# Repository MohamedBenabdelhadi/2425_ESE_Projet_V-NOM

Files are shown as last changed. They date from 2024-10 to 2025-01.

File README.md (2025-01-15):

# 2425-ESE-Projet-V-NOM

Ce projet consiste à créer un robot capable de jouer au chat et la souris avec d'autres robots du même type. Ils joueront sur une table sans bordures et devront donc être capable de détecter les bords de celle-ci.
Les élèves sont chargés de réaliser les schémas électroniques, le routage et la configuration des différents composants choisis pour réaliser ce projet.
Celui-ci est piloté par un microcontrôleur de type STM32.

> Groupe: Mohamed Benabdelhadi, Nouhaila Faris, Oliver Belliard, Valerian Priou.

## Strategie

La stratégie de déplacement retenue a été de détecter les bords de la surface de l'arène grâce à des capteurs de distance à l'avant du robot pointant chacun à 45° de l'axe central du robot, dans des directions opposées. L'idée d'origine consistait à mettre un capteur à l'avant et l'arrière mais suite aux conseils d'un intervenant extérieur, il a été jugé plus judicieux de placer les capteurs dans un même sens pour éviter que le robot tombe de la table dans les cas critiques, comme par exemple lorsque le robot s'approche du bord de la table avec une trajectoire diagonale avec un angle d'attaque très faible.  
  
**En mode souris :** le robot cherche à garder la plus grande distance possible du robot adverse ("chat"), tout en évitant les bords.  
**En mode chat :** le robot cherche à entrer en contact avec le robot adverse ("souris") par collision.  
  
La détection de la position du robot adverse se fait grâce au capteur Lidar qui permet de déterminer une trajectoire en temps réel. La détection de la collision est faite grâce à l'accéléromètre sur le PCB.  
  
Notre logique de direction consiste à réduire la différence entre l'angle où se trouve la cible détectée avec le Lidar puis s'approcher ou s'éloigner de celle ci en fonction du mode.  

## BOM (Bill Of Materials)

### Liste des composants

- Microcontrôleur : STM32G431CBU6 [(ST-Microelectronics)](https://www.st.com/en/microcontrollers-microprocessors/stm32g431cb.html)  
- Quartz 16 MHz [(Farnell : 2853935)](https://fr.farnell.com/multicomp/mcsjk-7u-16-00-10-30-80-b-30/quartz-16mhz-10pf-3-2mm-x-2-5mm/dp/2853935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)  
- Connecteur SWD/STLink [(Farnell : 3226055)](https://fr.farnell.com/harwin/m50-3600742/conn-btb-header-14-voies-2-rangs/dp/3226055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)  
- Driver moteur : ZXBM5210-SP-13 [(Farnell : 3946343)](https://ch.farnell.com/fr-CH/diodes-inc/zxbm5210-sp-13/motortreiber-40-bis-105-c/dp/3946343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)  
- Moteurs : DfRobot FIT0520 ou FIT0521 [(Farnell : 4308214)](https://fr.farnell.com/dfrobot/fit0521/motor-ducteur-cc-34-1-210rpm-6v/dp/4308214)  
- Accéléromètre : ADXL343BCCZ-RL [(Farnell : 4030100)](https://fr.farnell.com/analog-devices/adxl343bccz-rl/acc-l-rom-tre-mems-num-axes-x/dp/4030100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)  
- Régulateur 5V : MP1475S [(Farnell : 3357926)](https://fr.farnell.com/monolithic-power-systems-mps/mp1475sgj-p/conv-dc-dc-sync-buck-500khz-125/dp/3357926)  
- Régulateur 3.3V : BU33SD5WG-TR [(Farnell : 3011248)](https://fr.farnell.com/rohm/bu33sd5wg-tr/ldo-fixe-3-3v-0-5a-40-a-105-c/dp/3011248)  
- Batterie NIMH 7.2V 1.3Ah [(RS : 777-0377)](https://fr.rs-online.com/web/p/blocs-batteries-rechargeables/7770377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)  
- Capteur bordure : GP2Y0A41SK0F [(RS : 666-6568)](https://fr.rs-online.com/web/p/capteurs-optiques-reflechissants/6666568?gb=s)
- Lidar : [YDLIDAR X4](https://www.ydlidar.com/dowfile.html?cid=5&type=1)
- Connecteurs JST 2.54mm
- LED + R/C en 0603 :
  - LED Rouge : [(Farnell : 150060RS55040)](https://fr.farnell.com/wurth-elektronik/150060rs55040/led-rouge-90mcd-624nm-cms/dp/2900762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)
  - LED Verte : [(Farnell : 150060GS55040)](https://fr.farnell.com/wurth-elektronik/150060gs55040/led-verte-430mcd-525nm-cms/dp/2900760)
- Cable avec Connecteur du capteur de bordure : A03SR03SR30K152A [(Mouser : 306-A03SR03SR30K152A)](https://www.mouser.fr/ProductDetail/JST-Commercial/A03SR03SR30K152A?qs=QpmGXVUTftGJe7b%2B%2FlYZEQ%3D%3D)
- Port pour câble du capteur de bordure : BM03B-SRSS-TB(LF)(SN) [(Farnell : 1679128)](https://fr.farnell.com/jst-japan-solderless-terminals/bm03b-srss-tb-lf-sn/embase-entree-sur-le-dessus-3/dp/1679128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) *This product displays (LF)(SN) on the label to indicate RoHS compliance.* (JST_EH_S3B-EH_1x03_P2.50mm_Horizontal)
- Boutons poussoirs : [Wurth 430182070816] → empreinte KiCAD : SW Push 1P1T NO 6x6mm H9.5mm
- Interrupteur ON/OFF : [Wurth 472121020311] → empreinte à faire  
  
> **Fournisseurs autorisés :** RS, Farnell, Mouser.

### Sources d'empreintes

Pour les empreintes officielles (serveur utilisé par Farnell, Mouser...) : <https://componentsearchengine.com/>
> La création de compte est gratuite. <u> **/!\\**</u> La recherche et le téléchargement des empreintes composants doit se faire directement depuis le site et non pas depuis les sites de fournisseurs de composants pour éviter les bugs !

## Diagramme d'architecture

```mermaid
---
title: V-NOM
---

graph TD;
subgraph Robot
    subgraph PCB principal
        subgraph Déplacement
            D[Driver] -..-> Mot[Moteurs];
        end

        subgraph Contrôle
            M(("Microcontroleur fa:fa-twitter")) -- PWM --> D;
            Q[Quartz] ----> M;
        end

        subgraph Interface utilisateur
            M ----> LEDR[**Retour d'état :** LED Rouge, *mode chat*]
            M ----> LEDV[**Retour d'état :** LED Verte, *mode souris*]
            Bo[**Bouttons :** *switch* On/Off, Start, Mode] ----> M;
            Con[**Connecteur ST-Link :** Programmation/Debug, *debug* UART] ----> M;
        end

        subgraph Acquisition
            CD[**Détecter le bord :** Capteurs de distance] -- Analog --> M;
            L[**Détecter des robots environants :** Lidar] -- UART --> M;
            AG[**Détecter les mpacts et l'orientation :** Accéléromètre & Gyroscope] -- SPI / I2C --> M;
        end

        subgraph Déplacement
            Mot == Encodeur : 4 câbles ==> M;
        end

        subgraph Alimentation
            Batterie -- 7.2V --> R5V[Régulateur 5V : **Buck**];
            R5V -- 5V --> R3V[Régulateur 3.3V : **LDO**];

            R3V -- 3.3V --> M;
            R3V -- 3.3V --> AG;

            R5V -- 5V --> L;
            R5V -- 5V --> CD;
        end
    end
end
```

## Architecture du PCB

Notre PCB se présente de la forme suivante sous Kicad :  


L'architecture correspondante est la suivante :  


Nous avons divisé notre montage en 5 groupes : Acquisition, Interface Utilisateur, Controle, Alimentation et Deplacement.  
De cette façon on peut clairement distinguer les dépendances entre chaque groupe afin de mieux comprendre notre système.

## Test de l'ensemble

### Déplacement

Notre robot se déplaçait avec une différence de vitesse de rotation entre les deux moteurs mais nous avons pu corriger cela par la suite avec la commande PWM, de façon à ce que celui-ci avance de façon plus satisfaisante.
Voici deux vidéos que nous avons filmé du déplacement du robot sur la table :  

https://github.com/user-attachments/assets/6fe6b484-391f-4125-b6b6-b91c0b271807

Et sur le sol :

https://github.com/user-attachments/assets/b978a031-3b2a-425c-8a7f-36d00a8f8381

### Détection des bords

Le robot évite les bordures de la table en mesurant si une distance supérieure à 40 mm (distance entre les capteurs et la surface où repose le robot) des capteurs ToF est détectée.

Pour ce test, nous avons placé nos mains devant les capteurs à différentes distances pour faire varier les valeurs renvoyées par ces capteurs. C'est aussi de cette façon que nous avons dans un premier temps testé le comportement du robot en simulant les bords de table.  

WhatsApp Image 2025-01-10 at 08 03 31

Comme précisé plus tôt, nous avons choisi de mettre nos deux capteurs TOFs à l'avant de notre robot pour que celui-ci puisse différencier le cas où le bord de la table est proche de son côté gauche ou droit.  
Cela permet d'implémenter une réponse différente dans ces deux cas distincts et d'éviter les chutes accidentelles dues à une mauvaise manœuvre lors de la détection du bord de la table.

https://github.com/user-attachments/assets/6ce4b2a9-2457-454e-afb0-1f59e9b68249

Placer ces deux capteurs à l'avant permet de couvrir le cas où ceux-ci captent simultanément un bord, ou dans notre cas test, la présence de nos mains.

https://github.com/user-attachments/assets/8c24e3c7-2838-483b-800a-837b5c4522e4

Mis bout à bout, ces différentes réactions auraient permi au robot de longer le bord de la table grâce à une correction proportionnelle le jour de la démonstration.

### Le lidar

Le lidar envoie des données par DMA, on enregistre et on traite 1000 points à la fois, même si en réalité il ne mesure qu'un point par degré par tour. on traite alors les points mesurés lors d'environ 3 tours pour avoir une bonne résolution.  
Chaque point affiche la distance mesurée entre le Lidar et l'obstacle, avec l'angle correspondant à la différence d'angle avec l'axe frontal central du robot.

https://github.com/user-attachments/assets/2a43f50e-ff47-4074-a242-2cb1f4e33f11
  
Les informations reçues du Lidar sont comme le montre la capture ci dessous :  



### L'accéléromètre

A défaut de pouvoir nous servir de l'accéléromètre pour pouvoir détecter la collision avec d'autres robots par manque de temps, nous nous en sommes servi comme d'un bouton d'arrêt d'urgence, plus accessible que les boutons prévus à cet effet lorsque le robot est en mouvement sur la table.

https://github.com/user-attachments/assets/ef0c44d4-e8ed-4b50-9021-add47195b835

## Conclusion

Le point sur lequel nous avons rencontré le plus de problèmes concernait l'intégration.  
En prenant l'exemple du Lidar, nous n'avons jamais réussi à l'utiliser sur le robot sans erreurs de communication UART.  
  
On avait réussi à intégrer l'évitement des bords et le fait que notre robot suive une trajectoire en ligne droite la veille de la présentation. Mais en y travaillant davantage durant la nuit nous avons endommagé un régulateur lors de la mise sous tension du robot. Nous suspectons le câble d'un des deux moteurs d'avoir eu un faux contact.  
On a donc manqué de temps pour refaire fonctionner tout l'ensemble le lendemain, le matin de la démonstration, suite à de nouveaux dysfonctionnements et de nouvelles suspicions de faux-contact sur plusieurs câbles. Le sertissage de ceux-ci prenant beaucoup de temps, ainsi que le remplacement du régulateur, il nous a été physiquement impossible d'avoir une démonstration complète.  

Nous comptions nous servir de l'accéléromètre pour assurer la détection du contact avec un autre robot. Comme nous avons manqué de temps pour avoir un robot complètement fonctionnel jusque là, nous avons décidé de nous en servir comme une sorte de bouton d'arrêt en posant notre main sur le robot. En effet, nous nous étions rendu compte pendant les tests que le robot n'était pas si simple à arrêter une fois lancé, et que cette fonctionnalité était rapide à intégrer.  
  
Pour conclure, ce projet nous aura permis d'appliquer les différentes connaissances techniques acquises au cours de ce semestre, concernant les systèmes à microcontrôleurs, le design de PCB, la programmation en temps réel et la robotique. Ce projet nous aura aussi permis de développer notre travail d'équipe, que ce soit à travers la répartition des tâches, l'entraide ou encore par notre capacité à rester ouverts à des idées auxquelles on aurait pas pensé dans un premier temps.

---

## Astuces et solution à des erreurs courrantes

### Erreur de STM32CubeIDE recontré en Ubuntu 24 : libncurses5 missing
>
> Could not determine GDB version using command: /opt/st/stm32cubeide_1.2.0/plugins/com.st.stm32cube.ide.mcu.externaltools.gnu-tools-for-stm32.7-2018-q2-update.linux64_1.0.0.201904181610/tools/bin/arm-none-eabi-gdb --version

Source: [Reddit post: libncurses5-dev?](https://www.reddit.com/r/Ubuntu/comments/1cm97bg/libncurses5dev/). Issue: libncurses5 was removed in 24.04.

**Solution:**  

```bash
wget http://archive.ubuntu.com/ubuntu/pool/universe/n/ncurses/libtinfo5_6.4-2_amd64.deb && sudo dpkg -i libtinfo5_6.4-2_amd64.deb && rm -f libtinfo5_6.4-2_amd64.deb

wget http://archive.ubuntu.com/ubuntu/pool/universe/n/ncurses/libncurses5_6.4-2_amd64.deb && sudo dpkg -i libncurses5_6.4-2_amd64.deb && rm -f libncurses5_6.4-2_amd64.deb

sudo apt install lib32ncurses5-dev libncurses5 libncurses5-dev -y
```

### Mettre à jour une branche à partir de la branche principale (```main```)

```bash
git rebase master
```

### Se lancer avec le **protocole SPI** en STM32

C'est utile de regarder [le site officiel](https://wiki.st.com/stm32mcu/wiki/Getting_started_with_SPI#What_is_Serial_Peripheral_Interface_-28SPI-29--).
Quand STM32CubeIDE crash au démarage avec ue erreur `"Java" is not responding` il faut effacer le dossier nomé `.metadata` dans le répertoire workspace qui pose problème.

### Annuler un merge sur GitHub

Il faut resset la tête sur le commit juste avant la tête actuelle. Solution sur [Stack Overflow](https://stackoverflow.com/questions/42860234/how-to-undo-a-merge-in-github)

```bash
git checkout master
git reset --hard <commit_before_merge>
git push -f
```

Exemple :

```bash
git checkout master
git reset --hard master
git push -f
```

### Forcer un commit

Solution sur [Stack Overflow](https://stackoverflow.com/questions/448919/how-can-i-remove-a-commit-on-github)
On se remet sur la branche :

```bash
git rebase -i HEAD~2
```

Puis on force le push de la branche qu'on souhaite restaurer :

```bash
git push origin <branch_name> --force
```

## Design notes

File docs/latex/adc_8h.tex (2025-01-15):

\doxysection{/home/oliver/\+Documents/3\+A/2425\+\_\+\+ESE\+\_\+\+Projet\+\_\+\+V-\/\+NOM/\+Projet\+\_\+\+V-\/\+NOM\+\_\+\+STM32/\+Core/\+Inc/adc.h File Reference}
\hypertarget{adc_8h}{}\label{adc_8h}\index{/home/oliver/Documents/3A/2425\_ESE\_Projet\_V-\/NOM/Projet\_V-\/NOM\_STM32/Core/Inc/adc.h@{/home/oliver/Documents/3A/2425\_ESE\_Projet\_V-\/NOM/Projet\_V-\/NOM\_STM32/Core/Inc/adc.h}}

This file contains all the function prototypes for the \doxylink{adc_8c}{adc.\+c} file.  

{\ttfamily \#include "{}main.\+h"{}}\newline
Include dependency graph for adc.\+h\+:
% FIG 0
This graph shows which files directly or indirectly include this file\+:
% FIG 1
\doxysubsubsection*{Functions}
\begin{DoxyCompactItemize}
\item 
void \mbox{\hyperlink{adc_8h_acccd58aa70215a6b184ad242312ffd0c}{MX\+\_\+\+ADC1\+\_\+\+Init}} (void)
\end{DoxyCompactItemize}
\doxysubsubsection*{Variables}
\begin{DoxyCompactItemize}
\item 
ADC\+\_\+\+Handle\+Type\+Def \mbox{\hyperlink{adc_8h_a22b804736f5648d52f639b2647d4ed13}{hadc1}}
\end{DoxyCompactItemize}

\doxysubsection{Detailed Description}
This file contains all the function prototypes for the \doxylink{adc_8c}{adc.\+c} file. 

\begin{DoxyAttention}{Attention}

\end{DoxyAttention}
Copyright (c) 2024 STMicroelectronics. All rights reserved.

This software is licensed under terms that can be found in the LICENSE file in the root directory of this software component. If no LICENSE file comes with this software, it is provided AS-\/\+IS. 

Definition in file \mbox{\hyperlink{adc_8h_source}{adc.\+h}}.

\doxysubsection{Function Documentation}
\Hypertarget{adc_8h_acccd58aa70215a6b184ad242312ffd0c}\label{adc_8h_acccd58aa70215a6b184ad242312ffd0c} 
\index{adc.h@{adc.h}!MX\_ADC1\_Init@{MX\_ADC1\_Init}}
\index{MX\_ADC1\_Init@{MX\_ADC1\_Init}!adc.h@{adc.h}}
\doxysubsubsection{\texorpdfstring{MX\_ADC1\_Init()}{MX\_ADC1\_Init()}}
{\footnotesize\ttfamily void MX\+\_\+\+ADC1\+\_\+\+Init (\begin{DoxyParamCaption}\item[{void}]{ }\end{DoxyParamCaption})}

Common config

Configure the ADC multi-\/mode

Configure Regular Channel

Definition at line \mbox{\hyperlink{adc_8c_source_l00030}{30}} of file \mbox{\hyperlink{adc_8c_source}{adc.\+c}}.

Here is the call graph for this function\+:
% FIG 2
Here is the caller graph for this function\+:
% FIG 3

\doxysubsection{Variable Documentation}
\Hypertarget{adc_8h_a22b804736f5648d52f639b2647d4ed13}\label{adc_8h_a22b804736f5648d52f639b2647d4ed13} 
\index{adc.h@{adc.h}!hadc1@{hadc1}}
\index{hadc1@{hadc1}!adc.h@{adc.h}}
\doxysubsubsection{\texorpdfstring{hadc1}{hadc1}}
{\footnotesize\ttfamily ADC\+\_\+\+Handle\+Type\+Def hadc1\hspace{0.3cm}{\ttfamily [extern]}}

Definition at line \mbox{\hyperlink{adc_8c_source_l00027}{27}} of file \mbox{\hyperlink{adc_8c_source}{adc.\+c}}.

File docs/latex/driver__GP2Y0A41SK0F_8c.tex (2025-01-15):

\doxysection{/home/oliver/\+Documents/3\+A/2425\+\_\+\+ESE\+\_\+\+Projet\+\_\+\+V-\/\+NOM/\+Projet\+\_\+\+V-\/\+NOM\+\_\+\+STM32/\+Core/drivers/driver\+\_\+\+GP2\+Y0\+A41\+SK0F.c File Reference}
\hypertarget{driver__GP2Y0A41SK0F_8c}{}\label{driver__GP2Y0A41SK0F_8c}\index{/home/oliver/Documents/3A/2425\_ESE\_Projet\_V-\/NOM/Projet\_V-\/NOM\_STM32/Core/drivers/driver\_GP2Y0A41SK0F.c@{/home/oliver/Documents/3A/2425\_ESE\_Projet\_V-\/NOM/Projet\_V-\/NOM\_STM32/Core/drivers/driver\_GP2Y0A41SK0F.c}}
{\ttfamily \#include "{}driver\+\_\+\+GP2\+Y0\+A41\+SK0\+F.\+h"{}}\newline
{\ttfamily \#include "{}adc.\+h"{}}\newline
{\ttfamily \#include "{}gpio.\+h"{}}\newline
{\ttfamily \#include $<$stdio.\+h$>$}\newline
Include dependency graph for driver\+\_\+\+GP2\+Y0\+A41\+SK0\+F.\+c\+:
% FIG 0
\doxysubsubsection*{Functions}
\begin{DoxyCompactItemize}
\item 
void \mbox{\hyperlink{driver__GP2Y0A41SK0F_8c_aa7ad3e9907f6fb052aca0e5fd419485e}{GP2\+Y0\+A41\+SK0\+F\+\_\+\+Init}} (\mbox{\hyperlink{structh__GP2Y0A41SK0F__t}{h\+\_\+\+GP2\+Y0\+A41\+SK0\+F\+\_\+t}} \texorpdfstring{$\ast$}{*}htof)
\begin{DoxyCompactList}\small\item\em Initialize the GP2\+Y0\+A41\+SK0F sensors. \end{DoxyCompactList}\item 
void \mbox{\hyperlink{driver__GP2Y0A41SK0F_8c_a717bc3d5b29849d805ba7bb3db352d56}{GP2\+Y0\+A41\+SK0\+F\+\_\+\+Read\+\_\+\+To\+F1}} (\mbox{\hyperlink{structh__GP2Y0A41SK0F__t}{h\+\_\+\+GP2\+Y0\+A41\+SK0\+F\+\_\+t}} \texorpdfstring{$\ast$}{*}htof)
\begin{DoxyCompactList}\small\item\em Read raw ADC value from ToF sensor 1. \end{DoxyCompactList}\item 
void \mbox{\hyperlink{driver__GP2Y0A41SK0F_8c_ad0568e5c44844e6efc75a7dfe9f9d490}{GP2\+Y0\+A41\+SK0\+F\+\_\+\+Read\+\_\+\+To\+F2}} (\mbox{\hyperlink{structh__GP2Y0A41SK0F__t}{h\+\_\+\+GP2\+Y0\+A41\+SK0\+F\+\_\+t}} \texorpdfstring{$\ast$}{*}htof)
\begin{DoxyCompactList}\small\item\em Read raw ADC value from ToF sensor 2. \end{DoxyCompactList}\item 
void \mbox{\hyperlink{driver__GP2Y0A41SK0F_8c_a45360e44b7a7b368b4fa9ba584d6fb3a}{GP2\+Y0\+A41\+SK0\+F\+\_\+get\+\_\+distance}} (\mbox{\hyperlink{structh__GP2Y0A41SK0F__t}{h\+\_\+\+GP2\+Y0\+A41\+SK0\+F\+\_\+t}} \texorpdfstring{$\ast$}{*}htof)
\begin{DoxyCompactList}\small\item\em Compute distances for both ToF sensors based on ADC readings. \end{DoxyCompactList}\end{DoxyCompactItemize}

\doxysubsection{Function Documentation}
\Hypertarget{driver__GP2Y0A41SK0F_8c_a45360e44b7a7b368b4fa9ba584d6fb3a}\label{driver__GP2Y0A41SK0F_8c_a45360e44b7a7b368b4fa9ba584d6fb3a} 
\index{driver\_GP2Y0A41SK0F.c@{driver\_GP2Y0A41SK0F.c}!GP2Y0A41SK0F\_get\_distance@{GP2Y0A41SK0F\_get\_distance}}
\index{GP2Y0A41SK0F\_get\_distance@{GP2Y0A41SK0F\_get\_distance}!driver\_GP2Y0A41SK0F.c@{driver\_GP2Y0A41SK0F.c}}
\doxysubsubsection{\texorpdfstring{GP2Y0A41SK0F\_get\_distance()}{GP2Y0A41SK0F\_get\_distance()}}
{\footnotesize\ttfamily void GP2\+Y0\+A41\+SK0\+F\+\_\+get\+\_\+distance (\begin{DoxyParamCaption}\item[{\mbox{\hyperlink{structh__GP2Y0A41SK0F__t}{h\+\_\+\+GP2\+Y0\+A41\+SK0\+F\+\_\+t}} \texorpdfstring{$\ast$}{*}}]{htof }\end{DoxyParamCaption})}

Compute distances for both ToF sensors based on ADC readings. 

This function converts ADC values to distances in millimeters using a formula derived from the sensor datasheet.

\begin{DoxyParams}{Parameters}
{\em htof} & Pointer to the GP2\+Y0\+A41\+SK0F handle structure.\\
\hline
\end{DoxyParams}
\begin{DoxyWarning}{Warning}
\+:
\begin{DoxyItemize}
\item It expects to use a 12 bits ADC as an imput
\item it ranges from 35 mm to 400 mm @wource\+:
\item \href{https://github.com/sharpsensoruser/sharp-sensor-demos/blob/master/sharp_gp2y0a41sk0f_demo/sharp_gp2y0a41sk0f_demo.ino}{\texttt{ https\+://github.\+com/sharpsensoruser/sharp-\/sensor-\/demos/blob/master/sharp\+\_\+gp2y0a41sk0f\+\_\+demo/sharp\+\_\+gp2y0a41sk0f\+\_\+demo.\+ino}} 
\end{DoxyItemize}
\end{DoxyWarning}

Definition at line \mbox{\hyperlink{driver__GP2Y0A41SK0F_8c_source_l00089}{89}} of file \mbox{\hyperlink{driver__GP2Y0A41SK0F_8c_source}{driver\+\_\+\+GP2\+Y0\+A41\+SK0\+F.\+c}}.

Here is the call graph for this function\+:
% FIG 1
Here is the caller graph for this function\+:
% FIG 2
\Hypertarget{driver__GP2Y0A41SK0F_8c_aa7ad3e9907f6fb052aca0e5fd419485e}\label{driver__GP2Y0A41SK0F_8c_aa7ad3e9907f6fb052aca0e5fd419485e} 
\index{driver\_GP2Y0A41SK0F.c@{driver\_GP2Y0A41SK0F.c}!GP2Y0A41SK0F\_Init@{GP2Y0A41SK0F\_Init}}
\index{GP2Y0A41SK0F\_Init@{GP2Y0A41SK0F\_Init}!driver\_GP2Y0A41SK0F.c@{driver\_GP2Y0A41SK0F.c}}
\doxysubsubsection{\texorpdfstring{GP2Y0A41SK0F\_Init()}{GP2Y0A41SK0F\_Init()}}
{\footnotesize\ttfamily void GP2\+Y0\+A41\+SK0\+F\+\_\+\+Init (\begin{DoxyParamCaption}\item[{\mbox{\hyperlink{structh__GP2Y0A41SK0F__t}{h\+\_\+\+GP2\+Y0\+A41\+SK0\+F\+\_\+t}} \texorpdfstring{$\ast$}{*}}]{htof }\end{DoxyParamCaption})}

Initialize the GP2\+Y0\+A41\+SK0F sensors. 

\begin{DoxyParams}{Parameters}
{\em htof} & Pointer to the GP2\+Y0\+A41\+SK0F handle structure. \\
\hline
\end{DoxyParams}

Definition at line \mbox{\hyperlink{driver__GP2Y0A41SK0F_8c_source_l00018}{18}} of file \mbox{\hyperlink{driver__GP2Y0A41SK0F_8c_source}{driver\+\_\+\+GP2\+Y0\+A41\+SK0\+F.\+c}}.

Here is the call graph for this function\+:
% FIG 3
Here is the caller graph for this function\+:
% FIG 4
\Hypertarget{driver__GP2Y0A41SK0F_8c_a717bc3d5b29849d805ba7bb3db352d56}\label{driver__GP2Y0A41SK0F_8c_a717bc3d5b29849d805ba7bb3db352d56} 
\index{driver\_GP2Y0A41SK0F.c@{driver\_GP2Y0A41SK0F.c}!GP2Y0A41SK0F\_Read\_ToF1@{GP2Y0A41SK0F\_Read\_ToF1}}
\index{GP2Y0A41SK0F\_Read\_ToF1@{GP2Y0A41SK0F\_Read\_ToF1}!driver\_GP2Y0A41SK0F.c@{driver\_GP2Y0A41SK0F.c}}
\doxysubsubsection{\texorpdfstring{GP2Y0A41SK0F\_Read\_ToF1()}{GP2Y0A41SK0F\_Read\_ToF1()}}
{\footnotesize\ttfamily void GP2\+Y0\+A41\+SK0\+F\+\_\+\+Read\+\_\+\+To\+F1 (\begin{DoxyParamCaption}\item[{\mbox{\hyperlink{structh__GP2Y0A41SK0F__t}{h\+\_\+\+GP2\+Y0\+A41\+SK0\+F\+\_\+t}} \texorpdfstring{$\ast$}{*}}]{htof }\end{DoxyParamCaption})}

Read raw ADC value from ToF sensor 1. 

\begin{DoxyParams}{Parameters}
{\em htof} & Pointer to the GP2\+Y0\+A41\+SK0F handle structure. \\
\hline
\end{DoxyParams}

Definition at line \mbox{\hyperlink{driver__GP2Y0A41SK0F_8c_source_l00041}{41}} of file \mbox{\hyperlink{driver__GP2Y0A41SK0F_8c_source}{driver\+\_\+\+GP2\+Y0\+A41\+SK0\+F.\+c}}.

Here is the call graph for this function\+:
% FIG 5
Here is the caller graph for this function\+:
% FIG 6
\Hypertarget{driver__GP2Y0A41SK0F_8c_ad0568e5c44844e6efc75a7dfe9f9d490}\label{driver__GP2Y0A41SK0F_8c_ad0568e5c44844e6efc75a7dfe9f9d490} 
\index{driver\_GP2Y0A41SK0F.c@{driver\_GP2Y0A41SK0F.c}!GP2Y0A41SK0F\_Read\_ToF2@{GP2Y0A41SK0F\_Read\_ToF2}}
\index{GP2Y0A41SK0F\_Read\_ToF2@{GP2Y0A41SK0F\_Read\_ToF2}!driver\_GP2Y0A41SK0F.c@{driver\_GP2Y0A41SK0F.c}}
\doxysubsubsection{\texorpdfstring{GP2Y0A41SK0F\_Read\_ToF2()}{GP2Y0A41SK0F\_Read\_ToF2()}}
{\footnotesize\ttfamily void GP2\+Y0\+A41\+SK0\+F\+\_\+\+Read\+\_\+\+To\+F2 (\begin{DoxyParamCaption}\item[{\mbox{\hyperlink{structh__GP2Y0A41SK0F__t}{h\+\_\+\+GP2\+Y0\+A41\+SK0\+F\+\_\+t}} \texorpdfstring{$\ast$}{*}}]{htof }\end{DoxyParamCaption})}

Read raw ADC value from ToF sensor 2. 

\begin{DoxyParams}{Parameters}
{\em htof} & Pointer to the GP2\+Y0\+A41\+SK0F handle structure. \\
\hline
\end{DoxyParams}

Definition at line \mbox{\hyperlink{driver__GP2Y0A41SK0F_8c_source_l00061}{61}} of file \mbox{\hyperlink{driver__GP2Y0A41SK0F_8c_source}{driver\+\_\+\+GP2\+Y0\+A41\+SK0\+F.\+c}}.

Here is the call graph for this function\+:
% FIG 7
Here is the caller graph for this function\+:
% FIG 8

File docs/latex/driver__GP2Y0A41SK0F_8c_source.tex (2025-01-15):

\doxysection{driver\+\_\+\+GP2\+Y0\+A41\+SK0\+F.\+c}
\hypertarget{driver__GP2Y0A41SK0F_8c_source}{}\label{driver__GP2Y0A41SK0F_8c_source}\index{/home/oliver/Documents/3A/2425\_ESE\_Projet\_V-\/NOM/Projet\_V-\/NOM\_STM32/Core/drivers/driver\_GP2Y0A41SK0F.c@{/home/oliver/Documents/3A/2425\_ESE\_Projet\_V-\/NOM/Projet\_V-\/NOM\_STM32/Core/drivers/driver\_GP2Y0A41SK0F.c}}
\mbox{\hyperlink{driver__GP2Y0A41SK0F_8c}{Go to the documentation of this file.}}
\begin{DoxyCode}{0}
\DoxyCodeLine{\Hypertarget{driver__GP2Y0A41SK0F_8c_source_l00001}00001\ \textcolor{comment}{/*}}
\DoxyCodeLine{\Hypertarget{driver__GP2Y0A41SK0F_8c_source_l00002}00002\ \textcolor{comment}{\ *\ driver\_GP2Y0A41SK0F.c}}
\DoxyCodeLine{\Hypertarget{driver__GP2Y0A41SK0F_8c_source_l00003}00003\ \textcolor{comment}{\ *}}
\DoxyCodeLine{\Hypertarget{driver__GP2Y0A41SK0F_8c_source_l00004}00004\ \textcolor{comment}{\ *\ \ Created\ on:\ Oct\ 22,\ 2024}}
\DoxyCodeLine{\Hypertarget{driver__GP2Y0A41SK0F_8c_source_l00005}00005\ \textcolor{comment}{\ *\ \ \ \ \ \ Author:\ oliver}}
\DoxyCodeLine{\Hypertarget{driver__GP2Y0A41SK0F_8c_source_l00006}00006\ \textcolor{comment}{\ */}}
\DoxyCodeLine{\Hypertarget{driver__GP2Y0A41SK0F_8c_source_l00007}00007\ }
\DoxyCodeLine{\Hypertarget{driver__GP2Y0A41SK0F_8c_source_l00008}00008\ \textcolor{preprocessor}{\#include\ "{}\mbox{\hyperlink{driver__GP2Y0A41SK0F_8h}{driver\_GP2Y0A41SK0F.h}}"{}}}
\DoxyCodeLine{\Hypertarget{driver__GP2Y0A41SK0F_8c_source_l00009}00009\ \textcolor{preprocessor}{\#include\ "{}\mbox{\hyperlink{adc_8h}{adc.h}}"{}}}
\DoxyCodeLine{\Hypertarget{driver__GP2Y0A41SK0F_8c_source_l00010}00010\ \textcolor{preprocessor}{\#include\ "{}\mbox{\hyperlink{gpio_8h}{gpio.h}}"{}}}
\DoxyCodeLine{\Hypertarget{driver__GP2Y0A41SK0F_8c_source_l00011}00011\ \textcolor{preprocessor}{\#include\ <stdio.h>}}
\DoxyCodeLine{\Hypertarget{driver__GP2Y0A41SK0F_8c_source_l00012}00012\ }
\DoxyCodeLine{\Hypertarget{driver__GP2Y0A41SK0F_8c_source_l00013}00013\ }
\DoxyCodeLine{\Hypertarget{driver__GP2Y0A41SK0F_8c_source_l00018}\mbox{\hyperlink{driver__GP2Y0A41SK0F_8c_aa7ad3e9907f6fb052aca0e5fd419485e}{00018}}\ \textcolor{keywordtype}{void}\ \mbox{\hyperlink{driver__GP2Y0A41SK0F_8c_aa7ad3e9907f6fb052aca0e5fd419485e}{GP2Y0A41SK0F\_Init}}(\mbox{\hyperlink{structh__GP2Y0A41SK0F__t}{h\_GP2Y0A41SK0F\_t}}\ *\ htof)\ \{}
\DoxyCodeLine{\Hypertarget{driver__GP2Y0A41SK0F_8c_source_l00019}00019\ \ \ \ \ \textcolor{comment}{//\ The\ ADC\ used\ is\ wired\ on\ the\ board\ so\ it's\ ADC1}}
\DoxyCodeLine{\Hypertarget{driver__GP2Y0A41SK0F_8c_source_l00020}00020\ \ \ \ \ htof-\/>\mbox{\hyperlink{structh__GP2Y0A41SK0F__t_af982c0fe5d77061049c468b599100134}{hadc}}\ =\ \&\mbox{\hyperlink{adc_8h_a22b804736f5648d52f639b2647d4ed13}{hadc1}};}
\DoxyCodeLine{\Hypertarget{driver__GP2Y0A41SK0F_8c_source_l00021}00021\ }
\DoxyCodeLine{\Hypertarget{driver__GP2Y0A41SK0F_8c_source_l00022}00022\ \ \ \ \ \textcolor{keywordflow}{if}\ (HAL\_ADC\_Init(htof-\/>\mbox{\hyperlink{structh__GP2Y0A41SK0F__t_af982c0fe5d77061049c468b599100134}{hadc}})\ !=\ HAL\_OK)\ \{}
\DoxyCodeLine{\Hypertarget{driver__GP2Y0A41SK0F_8c_source_l00023}00023\ \ \ \ \ \ \ \ \ \mbox{\hyperlink{main_8h_a1730ffe1e560465665eb47d9264826f9}{Error\_Handler}}();}
\DoxyCodeLine{\Hypertarget{driver__GP2Y0A41SK0F_8c_source_l00024}00024\ \ \ \ \ \}}
\DoxyCodeLine{\Hypertarget{driver__GP2Y0A41SK0F_8c_source_l00025}00025\ }
\DoxyCodeLine{\Hypertarget{driver__GP2Y0A41SK0F_8c_source_l00026}00026\ \ \ \ \ \textcolor{comment}{//\ Channel\ Config\ ADC\ ToF1}}
\DoxyCodeLine{\Hypertarget{driver__GP2Y0A41SK0F_8c_source_l00027}00027\ \ \ \ \ htof-\/>\mbox{\hyperlink{structh__GP2Y0A41SK0F__t_a6a234707c2a0e0c0c2305eebb7d76f11}{cConfig\_tof1}}.Channel\ =\ ADC\_CHANNEL\_3;}
\DoxyCodeLine{\Hypertarget{driver__GP2Y0A41SK0F_8c_source_l00028}00028\ \ \ \ \ htof-\/>\mbox{\hyperlink{structh__GP2Y0A41SK0F__t_a6a234707c2a0e0c0c2305eebb7d76f11}{cConfig\_tof1}}.Rank\ =\ ADC\_REGULAR\_RANK\_1;}
\DoxyCodeLine{\Hypertarget{driver__GP2Y0A41SK0F_8c_source_l00029}00029\ \ \ \ \ htof-\/>\mbox{\hyperlink{structh__GP2Y0A41SK0F__t_a6a234707c2a0e0c0c2305eebb7d76f11}{cConfig\_tof1}}.SamplingTime\ =\ ADC\_SAMPLETIME\_47CYCLES\_5;}
\DoxyCodeLine{\Hypertarget{driver__GP2Y0A41SK0F_8c_source_l00030}00030\ }
\DoxyCodeLine{\Hypertarget{driver__GP2Y0A41SK0F_8c_source_l00031}00031\ \ \ \ \ \textcolor{comment}{//\ Channel\ Config\ ADC\ ToF2}}
\DoxyCodeLine{\Hypertarget{driver__GP2Y0A41SK0F_8c_source_l00032}00032\ \ \ \ \ htof-\/>\mbox{\hyperlink{structh__GP2Y0A41SK0F__t_a49d8eee2d2571b3ae0a696d0e6377d8e}{cConfig\_tof2}}.Channel\ =\ ADC\_CHANNEL\_1;}
\DoxyCodeLine{\Hypertarget{driver__GP2Y0A41SK0F_8c_source_l00033}00033\ \ \ \ \ htof-\/>\mbox{\hyperlink{structh__GP2Y0A41SK0F__t_a49d8eee2d2571b3ae0a696d0e6377d8e}{cConfig\_tof2}}.Rank\ =\ ADC\_REGULAR\_RANK\_1;}
\DoxyCodeLine{\Hypertarget{driver__GP2Y0A41SK0F_8c_source_l00034}00034\ \ \ \ \ htof-\/>\mbox{\hyperlink{structh__GP2Y0A41SK0F__t_a49d8eee2d2571b3ae0a696d0e6377d8e}{cConfig\_tof2}}.SamplingTime\ =\ ADC\_SAMPLETIME\_47CYCLES\_5;}
\DoxyCodeLine{\Hypertarget{driver__GP2Y0A41SK0F_8c_source_l00035}00035\ \}}
\DoxyCodeLine{\Hypertarget{driver__GP2Y0A41SK0F_8c_source_l00036}00036\ }
\DoxyCodeLine{\Hypertarget{driver__GP2Y0A41SK0F_8c_source_l00041}\mbox{\hyperlink{driver__GP2Y0A41SK0F_8c_a717bc3d5b29849d805ba7bb3db352d56}{00041}}\ \textcolor{keywordtype}{void}\ \mbox{\hyperlink{driver__GP2Y0A41SK0F_8c_a717bc3d5b29849d805ba7bb3db352d56}{GP2Y0A41SK0F\_Read\_ToF1}}(\mbox{\hyperlink{structh__GP2Y0A41SK0F__t}{h\_GP2Y0A41SK0F\_t}}\ *\ htof)}
\DoxyCodeLine{\Hypertarget{driver__GP2Y0A41SK0F_8c_source_l00042}00042\ \{}
\DoxyCodeLine{\Hypertarget{driver__GP2Y0A41SK0F_8c_source_l00043}00043\ \ \ \ \ \textcolor{keywordflow}{if}\ (HAL\_ADC\_ConfigChannel(htof-\/>\mbox{\hyperlink{structh__GP2Y0A41SK0F__t_af982c0fe5d77061049c468b599100134}{hadc}},\ \&htof-\/>\mbox{\hyperlink{structh__GP2Y0A41SK0F__t_a6a234707c2a0e0c0c2305eebb7d76f11}{cConfig\_tof1}})\ !=\ HAL\_OK)\ \{}
\DoxyCodeLine{\Hypertarget{driver__GP2Y0A41SK0F_8c_source_l00044}00044\ \ \ \ \ \ \ \ \ \mbox{\hyperlink{main_8h_a1730ffe1e560465665eb47d9264826f9}{Error\_Handler}}();}
\DoxyCodeLine{\Hypertarget{driver__GP2Y0A41SK0F_8c_source_l00045}00045\ \ \ \ \ \}}
\DoxyCodeLine{\Hypertarget{driver__GP2Y0A41SK0F_8c_source_l00046}00046\ }
\DoxyCodeLine{\Hypertarget{driver__GP2Y0A41SK0F_8c_source_l00047}00047\ \ \ \ \ HAL\_ADC\_Start(htof-\/>\mbox{\hyperlink{structh__GP2Y0A41SK0F__t_af982c0fe5d77061049c468b599100134}{hadc}});}
\DoxyCodeLine{\Hypertarget{driver__GP2Y0A41SK0F_8c_source_l00048}00048\ }
\DoxyCodeLine{\Hypertarget{driver__GP2Y0A41SK0F_8c_source_l00049}00049\ \ \ \ \ \textcolor{keywordflow}{if}\ (HAL\_ADC\_PollForConversion(htof-\/>\mbox{\hyperlink{structh__GP2Y0A41SK0F__t_af982c0fe5d77061049c468b599100134}{hadc}},\ HAL\_MAX\_DELAY)\ !=\ HAL\_OK)\ \{}
\DoxyCodeLine{\Hypertarget{driver__GP2Y0A41SK0F_8c_source_l00050}00050\ \ \ \ \ \ \ \ \ \mbox{\hyperlink{main_8h_a1730ffe1e560465665eb47d9264826f9}{Error\_Handler}}();}
\DoxyCodeLine{\Hypertarget{driver__GP2Y0A41SK0F_8c_source_l00051}00051\ \ \ \ \ \}}
\DoxyCodeLine{\Hypertarget{driver__GP2Y0A41SK0F_8c_source_l00052}00052\ }
\DoxyCodeLine{\Hypertarget{driver__GP2Y0A41SK0F_8c_source_l00053}00053\ \ \ \ \ htof-\/>\mbox{\hyperlink{structh__GP2Y0A41SK0F__t_a7fdc15c2ad2f480408312ff4135c9970}{adc\_val\_tof1}}\ =\ HAL\_ADC\_GetValue(htof-\/>\mbox{\hyperlink{structh__GP2Y0A41SK0F__t_af982c0fe5d77061049c468b599100134}{hadc}});}
\DoxyCodeLine{\Hypertarget{driver__GP2Y0A41SK0F_8c_source_l00054}00054\ \ \ \ \ HAL\_ADC\_Stop(htof-\/>\mbox{\hyperlink{structh__GP2Y0A41SK0F__t_af982c0fe5d77061049c468b599100134}{hadc}});}
\DoxyCodeLine{\Hypertarget{driver__GP2Y0A41SK0F_8c_source_l00055}00055\ \}}
\DoxyCodeLine{\Hypertarget{driver__GP2Y0A41SK0F_8c_source_l00056}00056\ }
\DoxyCodeLine{\Hypertarget{driver__GP2Y0A41SK0F_8c_source_l00061}\mbox{\hyperlink{driver__GP2Y0A41SK0F_8c_ad0568e5c44844e6efc75a7dfe9f9d490}{00061}}\ \textcolor{keywordtype}{void}\ \mbox{\hyperlink{driver__GP2Y0A41SK0F_8c_ad0568e5c44844e6efc75a7dfe9f9d490}{GP2Y0A41SK0F\_Read\_ToF2}}(\mbox{\hyperlink{structh__GP2Y0A41SK0F__t}{h\_GP2Y0A41SK0F\_t}}\ *\ htof)\ \{}
\DoxyCodeLine{\Hypertarget{driver__GP2Y0A41SK0F_8c_source_l00062}00062\ \ \ \ \ \textcolor{keywordflow}{if}\ (HAL\_ADC\_ConfigChannel(htof-\/>\mbox{\hyperlink{structh__GP2Y0A41SK0F__t_af982c0fe5d77061049c468b599100134}{hadc}},\ \&htof-\/>\mbox{\hyperlink{structh__GP2Y0A41SK0F__t_a49d8eee2d2571b3ae0a696d0e6377d8e}{cConfig\_tof2}})\ !=\ HAL\_OK)\ \{}
\DoxyCodeLine{\Hypertarget{driver__GP2Y0A41SK0F_8c_source_l00063}00063\ \ \ \ \ \ \ \ \ \mbox{\hyperlink{main_8h_a1730ffe1e560465665eb47d9264826f9}{Error\_Handler}}();}
\DoxyCodeLine{\Hypertarget{driver__GP2Y0A41SK0F_8c_source_l00064}00064\ \ \ \ \ \}}
\DoxyCodeLine{\Hypertarget{driver__GP2Y0A41SK0F_8c_source_l00065}00065\ \ \ \ \ HAL\_ADC\_Start(htof-\/>\mbox{\hyperlink{structh__GP2Y0A41SK0F__t_af982c0fe5d77061049c468b599100134}{hadc}});}
\DoxyCodeLine{\Hypertarget{driver__GP2Y0A41SK0F_8c_source_l00066}00066\ }
\DoxyCodeLine{\Hypertarget{driver__GP2Y0A41SK0F_8c_source_l00067}00067\ \ \ \ \ \textcolor{keywordflow}{if}\ (HAL\_ADC\_PollForConversion(htof-\/>\mbox{\hyperlink{structh__GP2Y0A41SK0F__t_af982c0fe5d77061049c468b599100134}{hadc}},\ HAL\_MAX\_DELAY)\ !=\ HAL\_OK)\ \{}
\DoxyCodeLine{\Hypertarget{driver__GP2Y0A41SK0F_8c_source_l00068}00068\ \ \ \ \ \ \ \ \ \mbox{\hyperlink{main_8h_a1730ffe1e560465665eb47d9264826f9}{Error\_Handler}}();}
\DoxyCodeLine{\Hypertarget{driver__GP2Y0A41SK0F_8c_source_l00069}00069\ \ \ \ \ \}}
\DoxyCodeLine{\Hypertarget{driver__GP2Y0A41SK0F_8c_source_l00070}00070\ }
\DoxyCodeLine{\Hypertarget{driver__GP2Y0A41SK0F_8c_source_l00071}00071\ \ \ \ \ htof-\/>\mbox{\hyperlink{structh__GP2Y0A41SK0F__t_aa9bd1e494692cd188986a8550db9350b}{adc\_val\_tof2}}\ =\ HAL\_ADC\_GetValue(htof-\/>\mbox{\hyperlink{structh__GP2Y0A41SK0F__t_af982c0fe5d77061049c468b599100134}{hadc}});}
\DoxyCodeLine{\Hypertarget{driver__GP2Y0A41SK0F_8c_source_l00072}00072\ \ \ \ \ HAL\_ADC\_Stop(htof-\/>\mbox{\hyperlink{structh__GP2Y0A41SK0F__t_af982c0fe5d77061049c468b599100134}{hadc}});}
\DoxyCodeLine{\Hypertarget{driver__GP2Y0A41SK0F_8c_source_l00073}00073\ \}}
\DoxyCodeLine{\Hypertarget{driver__GP2Y0A41SK0F_8c_source_l00074}00074\ }
\DoxyCodeLine{\Hypertarget{driver__GP2Y0A41SK0F_8c_source_l00089}\mbox{\hyperlink{driver__GP2Y0A41SK0F_8c_a45360e44b7a7b368b4fa9ba584d6fb3a}{00089}}\ \textcolor{keywordtype}{void}\ \mbox{\hyperlink{driver__GP2Y0A41SK0F_8c_a45360e44b7a7b368b4fa9ba584d6fb3a}{GP2Y0A41SK0F\_get\_distance}}(\mbox{\hyperlink{structh__GP2Y0A41SK0F__t}{h\_GP2Y0A41SK0F\_t}}\ *\ htof)}
\DoxyCodeLine{\Hypertarget{driver__GP2Y0A41SK0F_8c_source_l00090}00090\ \{}
\DoxyCodeLine{\Hypertarget{driver__GP2Y0A41SK0F_8c_source_l00091}00091\ \ \ \ \ \textcolor{comment}{//\ Convert\ to\ Distance\ in\ units\ of\ mm}}
\DoxyCodeLine{\Hypertarget{driver__GP2Y0A41SK0F_8c_source_l00092}00092\ \ \ \ \ \textcolor{comment}{//\ by\ approximating\ datasheet\ graph}}
\DoxyCodeLine{\Hypertarget{driver__GP2Y0A41SK0F_8c_source_l00093}00093\ \ \ \ \ \textcolor{comment}{//\ using\ equation\ of\ form:\ y\ =\ a/x\ +\ b}}
\DoxyCodeLine{\Hypertarget{driver__GP2Y0A41SK0F_8c_source_l00094}00094\ \ \ \ \ \textcolor{comment}{//\ and\ two\ (x,y)\ points\ on\ the\ graph:}}
\DoxyCodeLine{\Hypertarget{driver__GP2Y0A41SK0F_8c_source_l00095}00095\ \ \ \ \ \textcolor{comment}{//\ (35mm,\ 3V)\ and\ (400mm,\ 0.3V)}}
\DoxyCodeLine{\Hypertarget{driver__GP2Y0A41SK0F_8c_source_l00096}00096\ \ \ \ \ \textcolor{keyword}{const}\ \textcolor{keywordtype}{float}\ a\ =\ 120;}
\DoxyCodeLine{\Hypertarget{driver__GP2Y0A41SK0F_8c_source_l00097}00097\ \ \ \ \ \textcolor{keyword}{const}\ \textcolor{keywordtype}{float}\ b\ =\ 0.03;}
\DoxyCodeLine{\Hypertarget{driver__GP2Y0A41SK0F_8c_source_l00098}00098\ \ \ \ \ \textcolor{keywordtype}{float}\ Vo\ =\ 0;}
\DoxyCodeLine{\Hypertarget{driver__GP2Y0A41SK0F_8c_source_l00099}00099\ }
\DoxyCodeLine{\Hypertarget{driver__GP2Y0A41SK0F_8c_source_l00100}00100\ \ \ \ \ \mbox{\hyperlink{driver__GP2Y0A41SK0F_8c_a717bc3d5b29849d805ba7bb3db352d56}{GP2Y0A41SK0F\_Read\_ToF1}}(htof);}
\DoxyCodeLine{\Hypertarget{driver__GP2Y0A41SK0F_8c_source_l00101}00101\ \ \ \ \ \mbox{\hyperlink{driver__GP2Y0A41SK0F_8c_ad0568e5c44844e6efc75a7dfe9f9d490}{GP2Y0A41SK0F\_Read\_ToF2}}(htof);}
\DoxyCodeLine{\Hypertarget{driver__GP2Y0A41SK0F_8c_source_l00102}00102\ }
\DoxyCodeLine{\Hypertarget{driver__GP2Y0A41SK0F_8c_source_l00103}00103\ \ \ \ \ Vo\ =\ (\mbox{\hyperlink{driver__GP2Y0A41SK0F_8h_a1689d22b50ca895d410d0257bdf1d36c}{GP2Y0A41SK0F\_ADC\_VCC}}\ *\ htof-\/>\mbox{\hyperlink{structh__GP2Y0A41SK0F__t_a7fdc15c2ad2f480408312ff4135c9970}{adc\_val\_tof1}})\ /\ \mbox{\hyperlink{driver__GP2Y0A41SK0F_8h_aceb25d2d4176d0c88881b1fd42496fb6}{GP2Y0A41SK0F\_ADC\_MAX\_VALUE}};}
\DoxyCodeLine{\Hypertarget{driver__GP2Y0A41SK0F_8c_source_l00104}00104\ }
\DoxyCodeLine{\Hypertarget{driver__GP2Y0A41SK0F_8c_source_l00105}00105\ \ \ \ \ \textcolor{keywordflow}{if}\ (\ Vo\ >\ b\ )\ \{}
\DoxyCodeLine{\Hypertarget{driver__GP2Y0A41SK0F_8c_source_l00106}00106\ \ \ \ \ \ \ \ \ \textcolor{comment}{//\ Distance\ measured\ by\ ToF1\ in\ mm}}
\DoxyCodeLine{\Hypertarget{driver__GP2Y0A41SK0F_8c_source_l00107}00107\ \ \ \ \ \ \ \ \ htof-\/>\mbox{\hyperlink{structh__GP2Y0A41SK0F__t_aa1e82a003d8c3efe362e113d40d08e8d}{distance\_tof1}}\ =\ (int)(\ a\ /\ (Vo\ -\/\ b)\ );}
\DoxyCodeLine{\Hypertarget{driver__GP2Y0A41SK0F_8c_source_l00108}00108\ \ \ \ \ \}}
\DoxyCodeLine{\Hypertarget{driver__GP2Y0A41SK0F_8c_source_l00109}00109\ }
\DoxyCodeLine{\Hypertarget{driver__GP2Y0A41SK0F_8c_source_l00110}00110\ \ \ \ \ Vo\ =\ (\mbox{\hyperlink{driver__GP2Y0A41SK0F_8h_a1689d22b50ca895d410d0257bdf1d36c}{GP2Y0A41SK0F\_ADC\_VCC}}\ *\ htof-\/>\mbox{\hyperlink{structh__GP2Y0A41SK0F__t_aa9bd1e494692cd188986a8550db9350b}{adc\_val\_tof2}})\ /\ \mbox{\hyperlink{driver__GP2Y0A41SK0F_8h_aceb25d2d4176d0c88881b1fd42496fb6}{GP2Y0A41SK0F\_ADC\_MAX\_VALUE}};}
\DoxyCodeLine{\Hypertarget{driver__GP2Y0A41SK0F_8c_source_l00111}00111\ }
\DoxyCodeLine{\Hypertarget{driver__GP2Y0A41SK0F_8c_source_l00112}00112\ \ \ \ \ \textcolor{keywordflow}{if}\ (\ Vo\ >\ b\ )\ \{}
\DoxyCodeLine{\Hypertarget{driver__GP2Y0A41SK0F_8c_source_l00113}00113\ \ \ \ \ \ \ \ \ \textcolor{comment}{//\ Distance\ measured\ by\ ToF2\ in\ mm}}
\DoxyCodeLine{\Hypertarget{driver__GP2Y0A41SK0F_8c_source_l00114}00114\ \ \ \ \ \ \ \ \ htof-\/>\mbox{\hyperlink{structh__GP2Y0A41SK0F__t_a49f5b20a5cab5095c8aade8c4483638e}{distance\_tof2}}\ =\ (int)(\ a\ /\ (Vo\ -\/\ b)\ );}
\DoxyCodeLine{\Hypertarget{driver__GP2Y0A41SK0F_8c_source_l00115}00115\ \ \ \ \ \}}
\DoxyCodeLine{\Hypertarget{driver__GP2Y0A41SK0F_8c_source_l00116}00116\ \}}

\end{DoxyCode}

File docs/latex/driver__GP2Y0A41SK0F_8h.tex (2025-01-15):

\doxysection{/home/oliver/\+Documents/3\+A/2425\+\_\+\+ESE\+\_\+\+Projet\+\_\+\+V-\/\+NOM/\+Projet\+\_\+\+V-\/\+NOM\+\_\+\+STM32/\+Core/drivers/driver\+\_\+\+GP2\+Y0\+A41\+SK0F.h File Reference}
\hypertarget{driver__GP2Y0A41SK0F_8h}{}\label{driver__GP2Y0A41SK0F_8h}\index{/home/oliver/Documents/3A/2425\_ESE\_Projet\_V-\/NOM/Projet\_V-\/NOM\_STM32/Core/drivers/driver\_GP2Y0A41SK0F.h@{/home/oliver/Documents/3A/2425\_ESE\_Projet\_V-\/NOM/Projet\_V-\/NOM\_STM32/Core/drivers/driver\_GP2Y0A41SK0F.h}}
{\ttfamily \#include $<$stdlib.\+h$>$}\newline
{\ttfamily \#include $<$inttypes.\+h$>$}\newline
{\ttfamily \#include "{}adc.\+h"{}}\newline
Include dependency graph for driver\+\_\+\+GP2\+Y0\+A41\+SK0\+F.\+h\+:
% FIG 0
This graph shows which files directly or indirectly include this file\+:
% FIG 1
\doxysubsubsection*{Data Structures}
\begin{DoxyCompactItemize}
\item 
struct \mbox{\hyperlink{structh__GP2Y0A41SK0F__t}{h\+\_\+\+GP2\+Y0\+A41\+SK0\+F\+\_\+t}}
\begin{DoxyCompactList}\small\item\em Structure to handle GP2\+Y0\+A41\+SK0F sensor data and configurations. \end{DoxyCompactList}\end{DoxyCompactItemize}
\doxysubsubsection*{Macros}
\begin{DoxyCompactItemize}
\item 
\#define \mbox{\hyperlink{driver__GP2Y0A41SK0F_8h_a1689d22b50ca895d410d0257bdf1d36c}{GP2\+Y0\+A41\+SK0\+F\+\_\+\+ADC\+\_\+\+VCC}}~5.\+0
\item 
\#define \mbox{\hyperlink{driver__GP2Y0A41SK0F_8h_abfc41b989d0b4c4186dbfc17bfbd5a0c}{GP2\+Y0\+A41\+SK0\+F\+\_\+\+ADC\+\_\+\+BITS}}~12
\begin{DoxyCompactList}\small\item\em Number of ADC bits used. \end{DoxyCompactList}\item 
\#define \mbox{\hyperlink{driver__GP2Y0A41SK0F_8h_aceb25d2d4176d0c88881b1fd42496fb6}{GP2\+Y0\+A41\+SK0\+F\+\_\+\+ADC\+\_\+\+MAX\+\_\+\+VALUE}}~((1 $<$$<$ \mbox{\hyperlink{driver__GP2Y0A41SK0F_8h_abfc41b989d0b4c4186dbfc17bfbd5a0c}{GP2\+Y0\+A41\+SK0\+F\+\_\+\+ADC\+\_\+\+BITS}}) -\/ 1)
\begin{DoxyCompactList}\small\item\em Maximum ADC value. \end{DoxyCompactList}\end{DoxyCompactItemize}
\doxysubsubsection*{Functions}
\begin{DoxyCompactItemize}
\item 
void \mbox{\hyperlink{driver__GP2Y0A41SK0F_8h_aa7ad3e9907f6fb052aca0e5fd419485e}{GP2\+Y0\+A41\+SK0\+F\+\_\+\+Init}} (\mbox{\hyperlink{structh__GP2Y0A41SK0F__t}{h\+\_\+\+GP2\+Y0\+A41\+SK0\+F\+\_\+t}} \texorpdfstring{$\ast$}{*}htof)
\begin{DoxyCompactList}\small\item\em Initialize the GP2\+Y0\+A41\+SK0F sensors. \end{DoxyCompactList}\item 
void \mbox{\hyperlink{driver__GP2Y0A41SK0F_8h_a717bc3d5b29849d805ba7bb3db352d56}{GP2\+Y0\+A41\+SK0\+F\+\_\+\+Read\+\_\+\+To\+F1}} (\mbox{\hyperlink{structh__GP2Y0A41SK0F__t}{h\+\_\+\+GP2\+Y0\+A41\+SK0\+F\+\_\+t}} \texorpdfstring{$\ast$}{*}htof)
\begin{DoxyCompactList}\small\item\em Read raw ADC value from ToF sensor 1. \end{DoxyCompactList}\item 
void \mbox{\hyperlink{driver__GP2Y0A41SK0F_8h_ad0568e5c44844e6efc75a7dfe9f9d490}{GP2\+Y0\+A41\+SK0\+F\+\_\+\+Read\+\_\+\+To\+F2}} (\mbox{\hyperlink{structh__GP2Y0A41SK0F__t}{h\+\_\+\+GP2\+Y0\+A41\+SK0\+F\+\_\+t}} \texorpdfstring{$\ast$}{*}htof)
\begin{DoxyCompactList}\small\item\em Read raw ADC value from ToF sensor 2. \end{DoxyCompactList}\item 
void \mbox{\hyperlink{driver__GP2Y0A41SK0F_8h_a45360e44b7a7b368b4fa9ba584d6fb3a}{GP2\+Y0\+A41\+SK0\+F\+\_\+get\+\_\+distance}} (\mbox{\hyperlink{structh__GP2Y0A41SK0F__t}{h\+\_\+\+GP2\+Y0\+A41\+SK0\+F\+\_\+t}} \texorpdfstring{$\ast$}{*}htof)
\begin{DoxyCompactList}\small\item\em Compute distances for both ToF sensors based on ADC readings. \end{DoxyCompactList}\end{DoxyCompactItemize}

\doxysubsection{Macro Definition Documentation}
\Hypertarget{driver__GP2Y0A41SK0F_8h_abfc41b989d0b4c4186dbfc17bfbd5a0c}\label{driver__GP2Y0A41SK0F_8h_abfc41b989d0b4c4186dbfc17bfbd5a0c} 
\index{driver\_GP2Y0A41SK0F.h@{driver\_GP2Y0A41SK0F.h}!GP2Y0A41SK0F\_ADC\_BITS@{GP2Y0A41SK0F\_ADC\_BITS}}
\index{GP2Y0A41SK0F\_ADC\_BITS@{GP2Y0A41SK0F\_ADC\_BITS}!driver\_GP2Y0A41SK0F.h@{driver\_GP2Y0A41SK0F.h}}
\doxysubsubsection{\texorpdfstring{GP2Y0A41SK0F\_ADC\_BITS}{GP2Y0A41SK0F\_ADC\_BITS}}
{\footnotesize\ttfamily \#define GP2\+Y0\+A41\+SK0\+F\+\_\+\+ADC\+\_\+\+BITS~12}

Number of ADC bits used. 

Definition at line \mbox{\hyperlink{driver__GP2Y0A41SK0F_8h_source_l00013}{13}} of file \mbox{\hyperlink{driver__GP2Y0A41SK0F_8h_source}{driver\+\_\+\+GP2\+Y0\+A41\+SK0\+F.\+h}}.

\Hypertarget{driver__GP2Y0A41SK0F_8h_aceb25d2d4176d0c88881b1fd42496fb6}\label{driver__GP2Y0A41SK0F_8h_aceb25d2d4176d0c88881b1fd42496fb6} 
\index{driver\_GP2Y0A41SK0F.h@{driver\_GP2Y0A41SK0F.h}!GP2Y0A41SK0F\_ADC\_MAX\_VALUE@{GP2Y0A41SK0F\_ADC\_MAX\_VALUE}}
\index{GP2Y0A41SK0F\_ADC\_MAX\_VALUE@{GP2Y0A41SK0F\_ADC\_MAX\_VALUE}!driver\_GP2Y0A41SK0F.h@{driver\_GP2Y0A41SK0F.h}}
\doxysubsubsection{\texorpdfstring{GP2Y0A41SK0F\_ADC\_MAX\_VALUE}{GP2Y0A41SK0F\_ADC\_MAX\_VALUE}}
{\footnotesize\ttfamily \#define GP2\+Y0\+A41\+SK0\+F\+\_\+\+ADC\+\_\+\+MAX\+\_\+\+VALUE~((1 $<$$<$ \mbox{\hyperlink{driver__GP2Y0A41SK0F_8h_abfc41b989d0b4c4186dbfc17bfbd5a0c}{GP2\+Y0\+A41\+SK0\+F\+\_\+\+ADC\+\_\+\+BITS}}) -\/ 1)}

Maximum ADC value. 

Definition at line \mbox{\hyperlink{driver__GP2Y0A41SK0F_8h_source_l00014}{14}} of file \mbox{\hyperlink{driver__GP2Y0A41SK0F_8h_source}{driver\+\_\+\+GP2\+Y0\+A41\+SK0\+F.\+h}}.

\Hypertarget{driver__GP2Y0A41SK0F_8h_a1689d22b50ca895d410d0257bdf1d36c}\label{driver__GP2Y0A41SK0F_8h_a1689d22b50ca895d410d0257bdf1d36c} 
\index{driver\_GP2Y0A41SK0F.h@{driver\_GP2Y0A41SK0F.h}!GP2Y0A41SK0F\_ADC\_VCC@{GP2Y0A41SK0F\_ADC\_VCC}}
\index{GP2Y0A41SK0F\_ADC\_VCC@{GP2Y0A41SK0F\_ADC\_VCC}!driver\_GP2Y0A41SK0F.h@{driver\_GP2Y0A41SK0F.h}}
\doxysubsubsection{\texorpdfstring{GP2Y0A41SK0F\_ADC\_VCC}{GP2Y0A41SK0F\_ADC\_VCC}}
{\footnotesize\ttfamily \#define GP2\+Y0\+A41\+SK0\+F\+\_\+\+ADC\+\_\+\+VCC~5.\+0}

Definition at line \mbox{\hyperlink{driver__GP2Y0A41SK0F_8h_source_l00012}{12}} of file \mbox{\hyperlink{driver__GP2Y0A41SK0F_8h_source}{driver\+\_\+\+GP2\+Y0\+A41\+SK0\+F.\+h}}.

\doxysubsection{Function Documentation}
\Hypertarget{driver__GP2Y0A41SK0F_8h_a45360e44b7a7b368b4fa9ba584d6fb3a}\label{driver__GP2Y0A41SK0F_8h_a45360e44b7a7b368b4fa9ba584d6fb3a} 
\index{driver\_GP2Y0A41SK0F.h@{driver\_GP2Y0A41SK0F.h}!GP2Y0A41SK0F\_get\_distance@{GP2Y0A41SK0F\_get\_distance}}
\index{GP2Y0A41SK0F\_get\_distance@{GP2Y0A41SK0F\_get\_distance}!driver\_GP2Y0A41SK0F.h@{driver\_GP2Y0A41SK0F.h}}
\doxysubsubsection{\texorpdfstring{GP2Y0A41SK0F\_get\_distance()}{GP2Y0A41SK0F\_get\_distance()}}
{\footnotesize\ttfamily void GP2\+Y0\+A41\+SK0\+F\+\_\+get\+\_\+distance (\begin{DoxyParamCaption}\item[{\mbox{\hyperlink{structh__GP2Y0A41SK0F__t}{h\+\_\+\+GP2\+Y0\+A41\+SK0\+F\+\_\+t}} \texorpdfstring{$\ast$}{*}}]{htof }\end{DoxyParamCaption})}

Compute distances for both ToF sensors based on ADC readings. 

\begin{DoxyParams}{Parameters}
{\em htof} & Pointer to the GP2\+Y0\+A41\+SK0F handle structure.\\
\hline
\end{DoxyParams}
This function converts ADC values to distances in millimeters using a formula derived from the sensor datasheet.

\begin{DoxyParams}{Parameters}
{\em htof} & Pointer to the GP2\+Y0\+A41\+SK0F handle structure.\\
\hline
\end{DoxyParams}
\begin{DoxyWarning}{Warning}
\+:
\begin{DoxyItemize}
\item It expects to use a 12 bits ADC as an imput
\item it ranges from 35 mm to 400 mm @wource\+:
\item \href{https://github.com/sharpsensoruser/sharp-sensor-demos/blob/master/sharp_gp2y0a41sk0f_demo/sharp_gp2y0a41sk0f_demo.ino}{\texttt{ https\+://github.\+com/sharpsensoruser/sharp-\/sensor-\/demos/blob/master/sharp\+\_\+gp2y0a41sk0f\+\_\+demo/sharp\+\_\+gp2y0a41sk0f\+\_\+demo.\+ino}} 
\end{DoxyItemize}
\end{DoxyWarning}

Definition at line \mbox{\hyperlink{driver__GP2Y0A41SK0F_8c_source_l00089}{89}} of file \mbox{\hyperlink{driver__GP2Y0A41SK0F_8c_source}{driver\+\_\+\+GP2\+Y0\+A41\+SK0\+F.\+c}}.

Here is the call graph for this function\+:
% FIG 2
Here is the caller graph for this function\+:
% FIG 3
\Hypertarget{driver__GP2Y0A41SK0F_8h_aa7ad3e9907f6fb052aca0e5fd419485e}\label{driver__GP2Y0A41SK0F_8h_aa7ad3e9907f6fb052aca0e5fd419485e} 
\index{driver\_GP2Y0A41SK0F.h@{driver\_GP2Y0A41SK0F.h}!GP2Y0A41SK0F\_Init@{GP2Y0A41SK0F\_Init}}
\index{GP2Y0A41SK0F\_Init@{GP2Y0A41SK0F\_Init}!driver\_GP2Y0A41SK0F.h@{driver\_GP2Y0A41SK0F.h}}
\doxysubsubsection{\texorpdfstring{GP2Y0A41SK0F\_Init()}{GP2Y0A41SK0F\_Init()}}
{\footnotesize\ttfamily void GP2\+Y0\+A41\+SK0\+F\+\_\+\+Init (\begin{DoxyParamCaption}\item[{\mbox{\hyperlink{structh__GP2Y0A41SK0F__t}{h\+\_\+\+GP2\+Y0\+A41\+SK0\+F\+\_\+t}} \texorpdfstring{$\ast$}{*}}]{htof }\end{DoxyParamCaption})}

Initialize the GP2\+Y0\+A41\+SK0F sensors. 

\begin{DoxyParams}{Parameters}
{\em htof} & Pointer to the GP2\+Y0\+A41\+SK0F handle structure. \\
\hline
\end{DoxyParams}

Definition at line \mbox{\hyperlink{driver__GP2Y0A41SK0F_8c_source_l00018}{18}} of file \mbox{\hyperlink{driver__GP2Y0A41SK0F_8c_source}{driver\+\_\+\+GP2\+Y0\+A41\+SK0\+F.\+c}}.

Here is the call graph for this function\+:
% FIG 4
Here is the caller graph for this function\+:
% FIG 5
\Hypertarget{driver__GP2Y0A41SK0F_8h_a717bc3d5b29849d805ba7bb3db352d56}\label{driver__GP2Y0A41SK0F_8h_a717bc3d5b29849d805ba7bb3db352d56} 
\index{driver\_GP2Y0A41SK0F.h@{driver\_GP2Y0A41SK0F.h}!GP2Y0A41SK0F\_Read\_ToF1@{GP2Y0A41SK0F\_Read\_ToF1}}
\index{GP2Y0A41SK0F\_Read\_ToF1@{GP2Y0A41SK0F\_Read\_ToF1}!driver\_GP2Y0A41SK0F.h@{driver\_GP2Y0A41SK0F.h}}
\doxysubsubsection{\texorpdfstring{GP2Y0A41SK0F\_Read\_ToF1()}{GP2Y0A41SK0F\_Read\_ToF1()}}
{\footnotesize\ttfamily void GP2\+Y0\+A41\+SK0\+F\+\_\+\+Read\+\_\+\+To\+F1 (\begin{DoxyParamCaption}\item[{\mbox{\hyperlink{structh__GP2Y0A41SK0F__t}{h\+\_\+\+GP2\+Y0\+A41\+SK0\+F\+\_\+t}} \texorpdfstring{$\ast$}{*}}]{htof }\end{DoxyParamCaption})}

Read raw ADC value from ToF sensor 1. 

\begin{DoxyParams}{Parameters}
{\em htof} & Pointer to the GP2\+Y0\+A41\+SK0F handle structure. \\
\hline
\end{DoxyParams}

Definition at line \mbox{\hyperlink{driver__GP2Y0A41SK0F_8c_source_l00041}{41}} of file \mbox{\hyperlink{driver__GP2Y0A41SK0F_8c_source}{driver\+\_\+\+GP2\+Y0\+A41\+SK0\+F.\+c}}.

Here is the call graph for this function\+:
% FIG 6
Here is the caller graph for this function\+:
% FIG 7
\Hypertarget{driver__GP2Y0A41SK0F_8h_ad0568e5c44844e6efc75a7dfe9f9d490}\label{driver__GP2Y0A41SK0F_8h_ad0568e5c44844e6efc75a7dfe9f9d490} 
\index{driver\_GP2Y0A41SK0F.h@{driver\_GP2Y0A41SK0F.h}!GP2Y0A41SK0F\_Read\_ToF2@{GP2Y0A41SK0F\_Read\_ToF2}}
\index{GP2Y0A41SK0F\_Read\_ToF2@{GP2Y0A41SK0F\_Read\_ToF2}!driver\_GP2Y0A41SK0F.h@{driver\_GP2Y0A41SK0F.h}}
\doxysubsubsection{\texorpdfstring{GP2Y0A41SK0F\_Read\_ToF2()}{GP2Y0A41SK0F\_Read\_ToF2()}}
{\footnotesize\ttfamily void GP2\+Y0\+A41\+SK0\+F\+\_\+\+Read\+\_\+\+To\+F2 (\begin{DoxyParamCaption}\item[{\mbox{\hyperlink{structh__GP2Y0A41SK0F__t}{h\+\_\+\+GP2\+Y0\+A41\+SK0\+F\+\_\+t}} \texorpdfstring{$\ast$}{*}}]{htof }\end{DoxyParamCaption})}

Read raw ADC value from ToF sensor 2. 

\begin{DoxyParams}{Parameters}
{\em htof} & Pointer to the GP2\+Y0\+A41\+SK0F handle structure. \\
\hline
\end{DoxyParams}

Definition at line \mbox{\hyperlink{driver__GP2Y0A41SK0F_8c_source_l00061}{61}} of file \mbox{\hyperlink{driver__GP2Y0A41SK0F_8c_source}{driver\+\_\+\+GP2\+Y0\+A41\+SK0\+F.\+c}}.

Here is the call graph for this function\+:
% FIG 8
Here is the caller graph for this function\+:
% FIG 9

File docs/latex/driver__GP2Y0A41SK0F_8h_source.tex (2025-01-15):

\doxysection{driver\+\_\+\+GP2\+Y0\+A41\+SK0\+F.\+h}
\hypertarget{driver__GP2Y0A41SK0F_8h_source}{}\label{driver__GP2Y0A41SK0F_8h_source}\index{/home/oliver/Documents/3A/2425\_ESE\_Projet\_V-\/NOM/Projet\_V-\/NOM\_STM32/Core/drivers/driver\_GP2Y0A41SK0F.h@{/home/oliver/Documents/3A/2425\_ESE\_Projet\_V-\/NOM/Projet\_V-\/NOM\_STM32/Core/drivers/driver\_GP2Y0A41SK0F.h}}
\mbox{\hyperlink{driver__GP2Y0A41SK0F_8h}{Go to the documentation of this file.}}
\begin{DoxyCode}{0}
\DoxyCodeLine{\Hypertarget{driver__GP2Y0A41SK0F_8h_source_l00001}00001\ \textcolor{comment}{/*}}
\DoxyCodeLine{\Hypertarget{driver__GP2Y0A41SK0F_8h_source_l00002}00002\ \textcolor{comment}{\ *\ driver\_GP2Y0A41SK0F.h}}
\DoxyCodeLine{\Hypertarget{driver__GP2Y0A41SK0F_8h_source_l00003}00003\ \textcolor{comment}{\ *}}
\DoxyCodeLine{\Hypertarget{driver__GP2Y0A41SK0F_8h_source_l00004}00004\ \textcolor{comment}{\ *\ \ Created\ on:\ Oct\ 22,\ 2024}}
\DoxyCodeLine{\Hypertarget{driver__GP2Y0A41SK0F_8h_source_l00005}00005\ \textcolor{comment}{\ *\ \ \ \ \ \ Author:\ oliver}}
\DoxyCodeLine{\Hypertarget{driver__GP2Y0A41SK0F_8h_source_l00006}00006\ \textcolor{comment}{\ */}}
\DoxyCodeLine{\Hypertarget{driver__GP2Y0A41SK0F_8h_source_l00007}00007\ }
\DoxyCodeLine{\Hypertarget{driver__GP2Y0A41SK0F_8h_source_l00008}00008\ \textcolor{preprocessor}{\#include\ <stdlib.h>}}
\DoxyCodeLine{\Hypertarget{driver__GP2Y0A41SK0F_8h_source_l00009}00009\ \textcolor{preprocessor}{\#include\ <inttypes.h>}}
\DoxyCodeLine{\Hypertarget{driver__GP2Y0A41SK0F_8h_source_l00010}00010\ \textcolor{preprocessor}{\#include\ "{}\mbox{\hyperlink{adc_8h}{adc.h}}"{}}}
\DoxyCodeLine{\Hypertarget{driver__GP2Y0A41SK0F_8h_source_l00011}00011\ }
\DoxyCodeLine{\Hypertarget{driver__GP2Y0A41SK0F_8h_source_l00012}\mbox{\hyperlink{driver__GP2Y0A41SK0F_8h_a1689d22b50ca895d410d0257bdf1d36c}{00012}}\ \textcolor{preprocessor}{\#define\ GP2Y0A41SK0F\_ADC\_VCC\ 5.0}}
\DoxyCodeLine{\Hypertarget{driver__GP2Y0A41SK0F_8h_source_l00013}\mbox{\hyperlink{driver__GP2Y0A41SK0F_8h_abfc41b989d0b4c4186dbfc17bfbd5a0c}{00013}}\ \textcolor{preprocessor}{\#define\ GP2Y0A41SK0F\_ADC\_BITS\ 12\ }}
\DoxyCodeLine{\Hypertarget{driver__GP2Y0A41SK0F_8h_source_l00014}\mbox{\hyperlink{driver__GP2Y0A41SK0F_8h_aceb25d2d4176d0c88881b1fd42496fb6}{00014}}\ \textcolor{preprocessor}{\#define\ GP2Y0A41SK0F\_ADC\_MAX\_VALUE\ ((1\ <<\ GP2Y0A41SK0F\_ADC\_BITS)\ -\/\ 1)\ }}
\DoxyCodeLine{\Hypertarget{driver__GP2Y0A41SK0F_8h_source_l00015}00015\ }
\DoxyCodeLine{\Hypertarget{driver__GP2Y0A41SK0F_8h_source_l00016}00016\ }
\DoxyCodeLine{\Hypertarget{driver__GP2Y0A41SK0F_8h_source_l00020}\mbox{\hyperlink{structh__GP2Y0A41SK0F__t}{00020}}\ \textcolor{keyword}{typedef}\ \textcolor{keyword}{struct\ }\{}
\DoxyCodeLine{\Hypertarget{driver__GP2Y0A41SK0F_8h_source_l00021}\mbox{\hyperlink{structh__GP2Y0A41SK0F__t_af982c0fe5d77061049c468b599100134}{00021}}\ \ \ \ \ ADC\_HandleTypeDef\ *\mbox{\hyperlink{structh__GP2Y0A41SK0F__t_af982c0fe5d77061049c468b599100134}{hadc}};\ }
\DoxyCodeLine{\Hypertarget{driver__GP2Y0A41SK0F_8h_source_l00022}\mbox{\hyperlink{structh__GP2Y0A41SK0F__t_a6a234707c2a0e0c0c2305eebb7d76f11}{00022}}\ \ \ \ \ ADC\_ChannelConfTypeDef\ \mbox{\hyperlink{structh__GP2Y0A41SK0F__t_a6a234707c2a0e0c0c2305eebb7d76f11}{cConfig\_tof1}};\ }
\DoxyCodeLine{\Hypertarget{driver__GP2Y0A41SK0F_8h_source_l00023}\mbox{\hyperlink{structh__GP2Y0A41SK0F__t_a49d8eee2d2571b3ae0a696d0e6377d8e}{00023}}\ \ \ \ \ ADC\_ChannelConfTypeDef\ \mbox{\hyperlink{structh__GP2Y0A41SK0F__t_a49d8eee2d2571b3ae0a696d0e6377d8e}{cConfig\_tof2}};\ }
\DoxyCodeLine{\Hypertarget{driver__GP2Y0A41SK0F_8h_source_l00024}00024\ }
\DoxyCodeLine{\Hypertarget{driver__GP2Y0A41SK0F_8h_source_l00025}\mbox{\hyperlink{structh__GP2Y0A41SK0F__t_a7fdc15c2ad2f480408312ff4135c9970}{00025}}\ \ \ \ \ uint32\_t\ \mbox{\hyperlink{structh__GP2Y0A41SK0F__t_a7fdc15c2ad2f480408312ff4135c9970}{adc\_val\_tof1}};\ }
\DoxyCodeLine{\Hypertarget{driver__GP2Y0A41SK0F_8h_source_l00026}\mbox{\hyperlink{structh__GP2Y0A41SK0F__t_aa9bd1e494692cd188986a8550db9350b}{00026}}\ \ \ \ \ uint32\_t\ \mbox{\hyperlink{structh__GP2Y0A41SK0F__t_aa9bd1e494692cd188986a8550db9350b}{adc\_val\_tof2}};\ }
\DoxyCodeLine{\Hypertarget{driver__GP2Y0A41SK0F_8h_source_l00027}00027\ }
\DoxyCodeLine{\Hypertarget{driver__GP2Y0A41SK0F_8h_source_l00028}\mbox{\hyperlink{structh__GP2Y0A41SK0F__t_aa1e82a003d8c3efe362e113d40d08e8d}{00028}}\ \ \ \ \ \textcolor{keywordtype}{int}\ \mbox{\hyperlink{structh__GP2Y0A41SK0F__t_aa1e82a003d8c3efe362e113d40d08e8d}{distance\_tof1}};\ }
\DoxyCodeLine{\Hypertarget{driver__GP2Y0A41SK0F_8h_source_l00029}\mbox{\hyperlink{structh__GP2Y0A41SK0F__t_a49f5b20a5cab5095c8aade8c4483638e}{00029}}\ \ \ \ \ \textcolor{keywordtype}{int}\ \mbox{\hyperlink{structh__GP2Y0A41SK0F__t_a49f5b20a5cab5095c8aade8c4483638e}{distance\_tof2}};\ }
\DoxyCodeLine{\Hypertarget{driver__GP2Y0A41SK0F_8h_source_l00030}00030\ \}\ \mbox{\hyperlink{structh__GP2Y0A41SK0F__t}{h\_GP2Y0A41SK0F\_t}};}
\DoxyCodeLine{\Hypertarget{driver__GP2Y0A41SK0F_8h_source_l00031}00031\ }
\DoxyCodeLine{\Hypertarget{driver__GP2Y0A41SK0F_8h_source_l00032}00032\ }
\DoxyCodeLine{\Hypertarget{driver__GP2Y0A41SK0F_8h_source_l00037}00037\ \textcolor{keywordtype}{void}\ \mbox{\hyperlink{driver__GP2Y0A41SK0F_8h_aa7ad3e9907f6fb052aca0e5fd419485e}{GP2Y0A41SK0F\_Init}}(\mbox{\hyperlink{structh__GP2Y0A41SK0F__t}{h\_GP2Y0A41SK0F\_t}}\ *htof);}
\DoxyCodeLine{\Hypertarget{driver__GP2Y0A41SK0F_8h_source_l00038}00038\ }
\DoxyCodeLine{\Hypertarget{driver__GP2Y0A41SK0F_8h_source_l00043}00043\ \textcolor{keywordtype}{void}\ \mbox{\hyperlink{driver__GP2Y0A41SK0F_8h_a717bc3d5b29849d805ba7bb3db352d56}{GP2Y0A41SK0F\_Read\_ToF1}}(\mbox{\hyperlink{structh__GP2Y0A41SK0F__t}{h\_GP2Y0A41SK0F\_t}}\ *htof);}
\DoxyCodeLine{\Hypertarget{driver__GP2Y0A41SK0F_8h_source_l00044}00044\ }
\DoxyCodeLine{\Hypertarget{driver__GP2Y0A41SK0F_8h_source_l00049}00049\ \textcolor{keywordtype}{void}\ \mbox{\hyperlink{driver__GP2Y0A41SK0F_8h_ad0568e5c44844e6efc75a7dfe9f9d490}{GP2Y0A41SK0F\_Read\_ToF2}}(\mbox{\hyperlink{structh__GP2Y0A41SK0F__t}{h\_GP2Y0A41SK0F\_t}}\ *htof);}
\DoxyCodeLine{\Hypertarget{driver__GP2Y0A41SK0F_8h_source_l00050}00050\ }
\DoxyCodeLine{\Hypertarget{driver__GP2Y0A41SK0F_8h_source_l00055}00055\ \textcolor{keywordtype}{void}\ \mbox{\hyperlink{driver__GP2Y0A41SK0F_8h_a45360e44b7a7b368b4fa9ba584d6fb3a}{GP2Y0A41SK0F\_get\_distance}}(\mbox{\hyperlink{structh__GP2Y0A41SK0F__t}{h\_GP2Y0A41SK0F\_t}}\ *htof);}

\end{DoxyCode}

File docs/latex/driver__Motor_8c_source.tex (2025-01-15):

\doxysection{driver\+\_\+\+Motor.\+c}
\hypertarget{driver__Motor_8c_source}{}\label{driver__Motor_8c_source}\index{/home/oliver/Documents/3A/2425\_ESE\_Projet\_V-\/NOM/Projet\_V-\/NOM\_STM32/Core/drivers/driver\_Motor.c@{/home/oliver/Documents/3A/2425\_ESE\_Projet\_V-\/NOM/Projet\_V-\/NOM\_STM32/Core/drivers/driver\_Motor.c}}
\mbox{\hyperlink{driver__Motor_8c}{Go to the documentation of this file.}}
\begin{DoxyCode}{0}
\DoxyCodeLine{\Hypertarget{driver__Motor_8c_source_l00001}00001\ }
\DoxyCodeLine{\Hypertarget{driver__Motor_8c_source_l00006}00006\ \textcolor{preprocessor}{\#include\ "{}\mbox{\hyperlink{driver__Motor_8h}{driver\_Motor.h}}"{}}}
\DoxyCodeLine{\Hypertarget{driver__Motor_8c_source_l00007}00007\ \textcolor{preprocessor}{\#include\ "{}\mbox{\hyperlink{tim_8h}{tim.h}}"{}}\ \ \textcolor{comment}{//\ Inclusion\ for\ access\ to\ timers}}
\DoxyCodeLine{\Hypertarget{driver__Motor_8c_source_l00008}00008\ \textcolor{preprocessor}{\#include\ <stdio.h>}}
\DoxyCodeLine{\Hypertarget{driver__Motor_8c_source_l00009}00009\ }
\DoxyCodeLine{\Hypertarget{driver__Motor_8c_source_l00010}\mbox{\hyperlink{driver__Motor_8c_ad72dbcf6d0153db1b8d8a58001feed83}{00010}}\ \textcolor{preprocessor}{\#define\ DEBUG\ 0\ }}
\DoxyCodeLine{\Hypertarget{driver__Motor_8c_source_l00012}00012\ \textcolor{preprocessor}{\#if\ DEBUG}}
\DoxyCodeLine{\Hypertarget{driver__Motor_8c_source_l00013}00013\ \textcolor{preprocessor}{\#define\ DEBUG\_PRINT(...)\ printf(\_\_VA\_ARGS\_\_)}}
\DoxyCodeLine{\Hypertarget{driver__Motor_8c_source_l00014}00014\ \textcolor{preprocessor}{\#else}}
\DoxyCodeLine{\Hypertarget{driver__Motor_8c_source_l00015}\mbox{\hyperlink{driver__Motor_8c_a88edd2aa4feabff4af21a997d5d8aa23}{00015}}\ \textcolor{preprocessor}{\#define\ DEBUG\_PRINT(...)}}
\DoxyCodeLine{\Hypertarget{driver__Motor_8c_source_l00016}00016\ \textcolor{preprocessor}{\#endif}}
\DoxyCodeLine{\Hypertarget{driver__Motor_8c_source_l00017}00017\ }
\DoxyCodeLine{\Hypertarget{driver__Motor_8c_source_l00018}00018\ }
\DoxyCodeLine{\Hypertarget{driver__Motor_8c_source_l00024}\mbox{\hyperlink{driver__Motor_8c_ad1dfbf8ee0a807290e2030e9792ef959}{00024}}\ \textcolor{keywordtype}{void}\ \mbox{\hyperlink{driver__Motor_8c_ad1dfbf8ee0a807290e2030e9792ef959}{Motor\_Init}}(\mbox{\hyperlink{structh__Motor__t}{h\_Motor\_t}}\ *\ \mbox{\hyperlink{main_8c_a0bcb687a2a521ee4b8f96671baa7f1f1}{hMotors}},\ TIM\_HandleTypeDef\ *\ htim)\ \{}
\DoxyCodeLine{\Hypertarget{driver__Motor_8c_source_l00025}00025\ \ \ \ \ \textcolor{comment}{//\ Allows\ to\ get\ direct\ parameters\ from\ the\ timer\ used}}
\DoxyCodeLine{\Hypertarget{driver__Motor_8c_source_l00026}00026\ \ \ \ \ \mbox{\hyperlink{main_8c_a0bcb687a2a521ee4b8f96671baa7f1f1}{hMotors}}-\/>\mbox{\hyperlink{structh__Motor__t_a5dc7d1c65997ccaed48a93a3f4ffc486}{htim}}\ =\ htim;}
\DoxyCodeLine{\Hypertarget{driver__Motor_8c_source_l00027}00027\ \ \ \ \ \mbox{\hyperlink{main_8c_a0bcb687a2a521ee4b8f96671baa7f1f1}{hMotors}}-\/>\mbox{\hyperlink{structh__Motor__t_a5a9eda21d5770e2629c31b5eddbe0dba}{speed\_increase\_rate1}}\ =\ 50;}
\DoxyCodeLine{\Hypertarget{driver__Motor_8c_source_l00028}00028\ \ \ \ \ \mbox{\hyperlink{main_8c_a0bcb687a2a521ee4b8f96671baa7f1f1}{hMotors}}-\/>\mbox{\hyperlink{structh__Motor__t_a3a2ab33027bcc09292944cceea755590}{speed\_increase\_rate2}}\ =\ 50;}
\DoxyCodeLine{\Hypertarget{driver__Motor_8c_source_l00029}00029\ }
\DoxyCodeLine{\Hypertarget{driver__Motor_8c_source_l00030}00030\ \ \ \ \ \_\_HAL\_RCC\_GPIOA\_CLK\_ENABLE();}
\DoxyCodeLine{\Hypertarget{driver__Motor_8c_source_l00031}00031\ \ \ \ \ \_\_HAL\_RCC\_GPIOB\_CLK\_ENABLE();}
\DoxyCodeLine{\Hypertarget{driver__Motor_8c_source_l00032}00032\ }
\DoxyCodeLine{\Hypertarget{driver__Motor_8c_source_l00033}00033\ \ \ \ \ \mbox{\hyperlink{tim_8h_ad1f9d42690163f73f73e5b820c81ca14}{MX\_TIM1\_Init}}();}
\DoxyCodeLine{\Hypertarget{driver__Motor_8c_source_l00034}00034\ \ \ \ \ \textcolor{comment}{//MX\_TIM2\_Init();}}
\DoxyCodeLine{\Hypertarget{driver__Motor_8c_source_l00035}00035\ }
\DoxyCodeLine{\Hypertarget{driver__Motor_8c_source_l00036}00036\ \ \ \ \ HAL\_TIM\_PWM\_Start(\mbox{\hyperlink{main_8c_a0bcb687a2a521ee4b8f96671baa7f1f1}{hMotors}}-\/>\mbox{\hyperlink{structh__Motor__t_a5dc7d1c65997ccaed48a93a3f4ffc486}{htim}},\ TIM\_CHANNEL\_1);}
\DoxyCodeLine{\Hypertarget{driver__Motor_8c_source_l00037}00037\ \ \ \ \ HAL\_TIM\_PWM\_Start(\mbox{\hyperlink{main_8c_a0bcb687a2a521ee4b8f96671baa7f1f1}{hMotors}}-\/>\mbox{\hyperlink{structh__Motor__t_a5dc7d1c65997ccaed48a93a3f4ffc486}{htim}},\ TIM\_CHANNEL\_2);}
\DoxyCodeLine{\Hypertarget{driver__Motor_8c_source_l00038}00038\ \ \ \ \ HAL\_TIMEx\_PWMN\_Start(\mbox{\hyperlink{main_8c_a0bcb687a2a521ee4b8f96671baa7f1f1}{hMotors}}-\/>\mbox{\hyperlink{structh__Motor__t_a5dc7d1c65997ccaed48a93a3f4ffc486}{htim}},\ TIM\_CHANNEL\_1);}
\DoxyCodeLine{\Hypertarget{driver__Motor_8c_source_l00039}00039\ \ \ \ \ HAL\_TIMEx\_PWMN\_Start(\mbox{\hyperlink{main_8c_a0bcb687a2a521ee4b8f96671baa7f1f1}{hMotors}}-\/>\mbox{\hyperlink{structh__Motor__t_a5dc7d1c65997ccaed48a93a3f4ffc486}{htim}},\ TIM\_CHANNEL\_2);}
\DoxyCodeLine{\Hypertarget{driver__Motor_8c_source_l00040}00040\ }
\DoxyCodeLine{\Hypertarget{driver__Motor_8c_source_l00041}00041\ \ \ \ \ \mbox{\hyperlink{main_8c_a0bcb687a2a521ee4b8f96671baa7f1f1}{hMotors}}-\/>\mbox{\hyperlink{structh__Motor__t_aacedbdb8cb4d02b7279b79c3c82c3bb1}{mode\_mot1}}\ =\ \mbox{\hyperlink{driver__Motor_8h_acf114e04f9a4c659c80ce0106398f85ca6cc2183e0159e2fcbdfd85156b263ec0}{STANDBY\_MODE}};}
\DoxyCodeLine{\Hypertarget{driver__Motor_8c_source_l00042}00042\ \ \ \ \ \mbox{\hyperlink{main_8c_a0bcb687a2a521ee4b8f96671baa7f1f1}{hMotors}}-\/>\mbox{\hyperlink{structh__Motor__t_a40847f19d30aafdc35322769d7849b38}{mode\_mot2}}\ =\ \mbox{\hyperlink{driver__Motor_8h_acf114e04f9a4c659c80ce0106398f85ca6cc2183e0159e2fcbdfd85156b263ec0}{STANDBY\_MODE}};}
\DoxyCodeLine{\Hypertarget{driver__Motor_8c_source_l00043}00043\ \ \ \ \ \mbox{\hyperlink{driver__Motor_8c_a3b02c81c2bf2acaa597535ee656afe16}{Motor\_SetMode}}(\mbox{\hyperlink{main_8c_a0bcb687a2a521ee4b8f96671baa7f1f1}{hMotors}});}
\DoxyCodeLine{\Hypertarget{driver__Motor_8c_source_l00044}00044\ \}}
\DoxyCodeLine{\Hypertarget{driver__Motor_8c_source_l00045}00045\ }
\DoxyCodeLine{\Hypertarget{driver__Motor_8c_source_l00050}\mbox{\hyperlink{driver__Motor_8c_a3b02c81c2bf2acaa597535ee656afe16}{00050}}\ \textcolor{keywordtype}{void}\ \mbox{\hyperlink{driver__Motor_8c_a3b02c81c2bf2acaa597535ee656afe16}{Motor\_SetMode}}(\mbox{\hyperlink{structh__Motor__t}{h\_Motor\_t}}\ *\ \mbox{\hyperlink{main_8c_a0bcb687a2a521ee4b8f96671baa7f1f1}{hMotors}})}
\DoxyCodeLine{\Hypertarget{driver__Motor_8c_source_l00051}00051\ \{}
\DoxyCodeLine{\Hypertarget{driver__Motor_8c_source_l00052}00052\ \ \ \ \ \textcolor{keywordflow}{switch}\ (\mbox{\hyperlink{main_8c_a0bcb687a2a521ee4b8f96671baa7f1f1}{hMotors}}-\/>\mbox{\hyperlink{structh__Motor__t_aacedbdb8cb4d02b7279b79c3c82c3bb1}{mode\_mot1}})\ \{}
\DoxyCodeLine{\Hypertarget{driver__Motor_8c_source_l00053}00053\ \ \ \ \ \textcolor{keywordflow}{case}\ \mbox{\hyperlink{driver__Motor_8h_acf114e04f9a4c659c80ce0106398f85cad1f6f09deeb1242535c57abee1c7a8ac}{FORWARD\_MODE}}:}
\DoxyCodeLine{\Hypertarget{driver__Motor_8c_source_l00054}00054\ \ \ \ \ \ \ \ \ \mbox{\hyperlink{driver__Motor_8c_a88edd2aa4feabff4af21a997d5d8aa23}{DEBUG\_PRINT}}(\textcolor{stringliteral}{"{}Mot1:\ FORWARD\_MODE\(\backslash\)r\(\backslash\)n"{}});}
\DoxyCodeLine{\Hypertarget{driver__Motor_8c_source_l00055}00055\ \ \ \ \ \ \ \ \ HAL\_TIM\_PWM\_Start(\mbox{\hyperlink{main_8c_a0bcb687a2a521ee4b8f96671baa7f1f1}{hMotors}}-\/>\mbox{\hyperlink{structh__Motor__t_a5dc7d1c65997ccaed48a93a3f4ffc486}{htim}},\ TIM\_CHANNEL\_1);}
\DoxyCodeLine{\Hypertarget{driver__Motor_8c_source_l00056}00056\ \ \ \ \ \ \ \ \ HAL\_TIMEx\_PWMN\_Stop(\mbox{\hyperlink{main_8c_a0bcb687a2a521ee4b8f96671baa7f1f1}{hMotors}}-\/>\mbox{\hyperlink{structh__Motor__t_a5dc7d1c65997ccaed48a93a3f4ffc486}{htim}},\ TIM\_CHANNEL\_1);}
\DoxyCodeLine{\Hypertarget{driver__Motor_8c_source_l00057}00057\ \ \ \ \ \ \ \ \ \textcolor{keywordflow}{break};}
\DoxyCodeLine{\Hypertarget{driver__Motor_8c_source_l00058}00058\ }
\DoxyCodeLine{\Hypertarget{driver__Motor_8c_source_l00059}00059\ \ \ \ \ \textcolor{keywordflow}{case}\ \mbox{\hyperlink{driver__Motor_8h_acf114e04f9a4c659c80ce0106398f85ca372ede0ca384ff46db46e8e76b955f30}{REVERSE\_MODE}}:}
\DoxyCodeLine{\Hypertarget{driver__Motor_8c_source_l00060}00060\ \ \ \ \ \ \ \ \ \mbox{\hyperlink{driver__Motor_8c_a88edd2aa4feabff4af21a997d5d8aa23}{DEBUG\_PRINT}}(\textcolor{stringliteral}{"{}Mot1:\ REVERSE\_MODE\(\backslash\)r\(\backslash\)n"{}});}
\DoxyCodeLine{\Hypertarget{driver__Motor_8c_source_l00061}00061\ \ \ \ \ \ \ \ \ HAL\_TIMEx\_PWMN\_Start(\mbox{\hyperlink{main_8c_a0bcb687a2a521ee4b8f96671baa7f1f1}{hMotors}}-\/>\mbox{\hyperlink{structh__Motor__t_a5dc7d1c65997ccaed48a93a3f4ffc486}{htim}},\ TIM\_CHANNEL\_1);}
\DoxyCodeLine{\Hypertarget{driver__Motor_8c_source_l00062}00062\ \ \ \ \ \ \ \ \ HAL\_TIM\_PWM\_Stop(\mbox{\hyperlink{main_8c_a0bcb687a2a521ee4b8f96671baa7f1f1}{hMotors}}-\/>\mbox{\hyperlink{structh__Motor__t_a5dc7d1c65997ccaed48a93a3f4ffc486}{htim}},\ TIM\_CHANNEL\_1);}
\DoxyCodeLine{\Hypertarget{driver__Motor_8c_source_l00063}00063\ \ \ \ \ \ \ \ \ \textcolor{keywordflow}{break};}
\DoxyCodeLine{\Hypertarget{driver__Motor_8c_source_l00064}00064\ }
\DoxyCodeLine{\Hypertarget{driver__Motor_8c_source_l00065}00065\ \ \ \ \ \textcolor{keywordflow}{case}\ \mbox{\hyperlink{driver__Motor_8h_acf114e04f9a4c659c80ce0106398f85ca6cc2183e0159e2fcbdfd85156b263ec0}{STANDBY\_MODE}}:}
\DoxyCodeLine{\Hypertarget{driver__Motor_8c_source_l00066}00066\ \ \ \ \ \textcolor{keywordflow}{default}:}
\DoxyCodeLine{\Hypertarget{driver__Motor_8c_source_l00067}00067\ \ \ \ \ \ \ \ \ HAL\_TIMEx\_PWMN\_Stop(\mbox{\hyperlink{main_8c_a0bcb687a2a521ee4b8f96671baa7f1f1}{hMotors}}-\/>\mbox{\hyperlink{structh__Motor__t_a5dc7d1c65997ccaed48a93a3f4ffc486}{htim}},\ TIM\_CHANNEL\_1);}
\DoxyCodeLine{\Hypertarget{driver__Motor_8c_source_l00068}00068\ \ \ \ \ \ \ \ \ HAL\_TIM\_PWM\_Stop(\mbox{\hyperlink{main_8c_a0bcb687a2a521ee4b8f96671baa7f1f1}{hMotors}}-\/>\mbox{\hyperlink{structh__Motor__t_a5dc7d1c65997ccaed48a93a3f4ffc486}{htim}},\ TIM\_CHANNEL\_1);}
\DoxyCodeLine{\Hypertarget{driver__Motor_8c_source_l00069}00069\ \ \ \ \ \ \ \ \ \_\_HAL\_TIM\_SET\_COMPARE(\mbox{\hyperlink{main_8c_a0bcb687a2a521ee4b8f96671baa7f1f1}{hMotors}}-\/>\mbox{\hyperlink{structh__Motor__t_a5dc7d1c65997ccaed48a93a3f4ffc486}{htim}},\ TIM\_CHANNEL\_1,\ 0);}
\DoxyCodeLine{\Hypertarget{driver__Motor_8c_source_l00070}00070\ \ \ \ \ \ \ \ \ \textcolor{keywordflow}{break};}
\DoxyCodeLine{\Hypertarget{driver__Motor_8c_source_l00071}00071\ \ \ \ \ \}}
\DoxyCodeLine{\Hypertarget{driver__Motor_8c_source_l00072}00072\ }
\DoxyCodeLine{\Hypertarget{driver__Motor_8c_source_l00073}00073\ \ \ \ \ \textcolor{keywordflow}{switch}\ (\mbox{\hyperlink{main_8c_a0bcb687a2a521ee4b8f96671baa7f1f1}{hMotors}}-\/>\mbox{\hyperlink{structh__Motor__t_a40847f19d30aafdc35322769d7849b38}{mode\_mot2}})\ \{}
\DoxyCodeLine{\Hypertarget{driver__Motor_8c_source_l00074}00074\ \ \ \ \ \textcolor{keywordflow}{case}\ \mbox{\hyperlink{driver__Motor_8h_acf114e04f9a4c659c80ce0106398f85cad1f6f09deeb1242535c57abee1c7a8ac}{FORWARD\_MODE}}:}
\DoxyCodeLine{\Hypertarget{driver__Motor_8c_source_l00075}00075\ \ \ \ \ \ \ \ \ \mbox{\hyperlink{driver__Motor_8c_a88edd2aa4feabff4af21a997d5d8aa23}{DEBUG\_PRINT}}(\textcolor{stringliteral}{"{}Mot2:\ FORWARD\_MODE\(\backslash\)r\(\backslash\)n"{}});}
\DoxyCodeLine{\Hypertarget{driver__Motor_8c_source_l00076}00076\ \ \ \ \ \ \ \ \ HAL\_TIM\_PWM\_Start(\mbox{\hyperlink{main_8c_a0bcb687a2a521ee4b8f96671baa7f1f1}{hMotors}}-\/>\mbox{\hyperlink{structh__Motor__t_a5dc7d1c65997ccaed48a93a3f4ffc486}{htim}},\ TIM\_CHANNEL\_2);}
\DoxyCodeLine{\Hypertarget{driver__Motor_8c_source_l00077}00077\ \ \ \ \ \ \ \ \ HAL\_TIMEx\_PWMN\_Stop(\mbox{\hyperlink{main_8c_a0bcb687a2a521ee4b8f96671baa7f1f1}{hMotors}}-\/>\mbox{\hyperlink{structh__Motor__t_a5dc7d1c65997ccaed48a93a3f4ffc486}{htim}},\ TIM\_CHANNEL\_2);}
\DoxyCodeLine{\Hypertarget{driver__Motor_8c_source_l00078}00078\ \ \ \ \ \ \ \ \ \textcolor{keywordflow}{break};}
\DoxyCodeLine{\Hypertarget{driver__Motor_8c_source_l00079}00079\ }
\DoxyCodeLine{\Hypertarget{driver__Motor_8c_source_l00080}00080\ \ \ \ \ \textcolor{keywordflow}{case}\ \mbox{\hyperlink{driver__Motor_8h_acf114e04f9a4c659c80ce0106398f85ca372ede0ca384ff46db46e8e76b955f30}{REVERSE\_MODE}}:}
\DoxyCodeLine{\Hypertarget{driver__Motor_8c_source_l00081}00081\ \ \ \ \ \ \ \ \ \mbox{\hyperlink{driver__Motor_8c_a88edd2aa4feabff4af21a997d5d8aa23}{DEBUG\_PRINT}}(\textcolor{stringliteral}{"{}Mot2:\ REVERSE\_MODE\(\backslash\)r\(\backslash\)n"{}});}
\DoxyCodeLine{\Hypertarget{driver__Motor_8c_source_l00082}00082\ \ \ \ \ \ \ \ \ HAL\_TIMEx\_PWMN\_Start(\mbox{\hyperlink{main_8c_a0bcb687a2a521ee4b8f96671baa7f1f1}{hMotors}}-\/>\mbox{\hyperlink{structh__Motor__t_a5dc7d1c65997ccaed48a93a3f4ffc486}{htim}},\ TIM\_CHANNEL\_2);}
\DoxyCodeLine{\Hypertarget{driver__Motor_8c_source_l00083}00083\ \ \ \ \ \ \ \ \ HAL\_TIM\_PWM\_Stop(\mbox{\hyperlink{main_8c_a0bcb687a2a521ee4b8f96671baa7f1f1}{hMotors}}-\/>\mbox{\hyperlink{structh__Motor__t_a5dc7d1c65997ccaed48a93a3f4ffc486}{htim}},\ TIM\_CHANNEL\_2);}
\DoxyCodeLine{\Hypertarget{driver__Motor_8c_source_l00084}00084\ \ \ \ \ \ \ \ \ \textcolor{keywordflow}{break};}
\DoxyCodeLine{\Hypertarget{driver__Motor_8c_source_l00085}00085\ }
\DoxyCodeLine{\Hypertarget{driver__Motor_8c_source_l00086}00086\ \ \ \ \ \textcolor{keywordflow}{case}\ \mbox{\hyperlink{driver__Motor_8h_acf114e04f9a4c659c80ce0106398f85ca6cc2183e0159e2fcbdfd85156b263ec0}{STANDBY\_MODE}}:}
\DoxyCodeLine{\Hypertarget{driver__Motor_8c_source_l00087}00087\ \ \ \ \ \textcolor{keywordflow}{default}:}
\DoxyCodeLine{\Hypertarget{driver__Motor_8c_source_l00088}00088\ \ \ \ \ \ \ \ \ HAL\_TIMEx\_PWMN\_Stop(\mbox{\hyperlink{main_8c_a0bcb687a2a521ee4b8f96671baa7f1f1}{hMotors}}-\/>\mbox{\hyperlink{structh__Motor__t_a5dc7d1c65997ccaed48a93a3f4ffc486}{htim}},\ TIM\_CHANNEL\_2);}
\DoxyCodeLine{\Hypertarget{driver__Motor_8c_source_l00089}00089\ \ \ \ \ \ \ \ \ HAL\_TIM\_PWM\_Stop(\mbox{\hyperlink{main_8c_a0bcb687a2a521ee4b8f96671baa7f1f1}{hMotors}}-\/>\mbox{\hyperlink{structh__Motor__t_a5dc7d1c65997ccaed48a93a3f4ffc486}{htim}},\ TIM\_CHANNEL\_2);}
\DoxyCodeLine{\Hypertarget{driver__Motor_8c_source_l00090}00090\ \ \ \ \ \ \ \ \ \_\_HAL\_TIM\_SET\_COMPARE(\mbox{\hyperlink{main_8c_a0bcb687a2a521ee4b8f96671baa7f1f1}{hMotors}}-\/>\mbox{\hyperlink{structh__Motor__t_a5dc7d1c65997ccaed48a93a3f4ffc486}{htim}},\ TIM\_CHANNEL\_2,\ 0);}
\DoxyCodeLine{\Hypertarget{driver__Motor_8c_source_l00091}00091\ \ \ \ \ \ \ \ \ \textcolor{keywordflow}{break};}
\DoxyCodeLine{\Hypertarget{driver__Motor_8c_source_l00092}00092\ \ \ \ \ \}}
\DoxyCodeLine{\Hypertarget{driver__Motor_8c_source_l00093}00093\ \}}
\DoxyCodeLine{\Hypertarget{driver__Motor_8c_source_l00094}00094\ }
\DoxyCodeLine{\Hypertarget{driver__Motor_8c_source_l00101}\mbox{\hyperlink{driver__Motor_8c_a99e002085849d62c67a8c049a9e18f68}{00101}}\ \textcolor{keywordtype}{void}\ \mbox{\hyperlink{driver__Motor_8c_a99e002085849d62c67a8c049a9e18f68}{Motor\_SetSpeed\_percent}}(\mbox{\hyperlink{structh__Motor__t}{h\_Motor\_t}}\ *\ hMotor,\ \textcolor{keywordtype}{float}\ percent1,\ \textcolor{keywordtype}{float}\ percent2)\ \{}
\DoxyCodeLine{\Hypertarget{driver__Motor_8c_source_l00102}00102\ \ \ \ \ hMotor-\/>\mbox{\hyperlink{structh__Motor__t_a8df75e44122e148783e198e3e81691ee}{speed1}}\ =\ (int)(\mbox{\hyperlink{driver__Motor_8h_a7ceb9a76bf36e33f3d1543c522ec6fa4}{MOTOR1\_REV\_DIFF}}\ *\ hMotor-\/>\mbox{\hyperlink{structh__Motor__t_a5dc7d1c65997ccaed48a93a3f4ffc486}{htim}}-\/>Init.Period\ *\ percent1/100.0);}
\DoxyCodeLine{\Hypertarget{driver__Motor_8c_source_l00103}00103\ \ \ \ \ hMotor-\/>\mbox{\hyperlink{structh__Motor__t_ab84050b626016809de350970d5006968}{speed2}}\ =\ (int)(hMotor-\/>\mbox{\hyperlink{structh__Motor__t_a5dc7d1c65997ccaed48a93a3f4ffc486}{htim}}-\/>Init.Period\ *\ percent2/100.0);}
\DoxyCodeLine{\Hypertarget{driver__Motor_8c_source_l00104}00104\ \}}
\DoxyCodeLine{\Hypertarget{driver__Motor_8c_source_l00105}00105\ }
\DoxyCodeLine{\Hypertarget{driver__Motor_8c_source_l00110}\mbox{\hyperlink{driver__Motor_8c_a7af54401c99ac93f3e732bca464837f1}{00110}}\ \textcolor{keywordtype}{void}\ \mbox{\hyperlink{driver__Motor_8c_a7af54401c99ac93f3e732bca464837f1}{Motor\_Stop}}(\mbox{\hyperlink{structh__Motor__t}{h\_Motor\_t}}\ *\ \mbox{\hyperlink{main_8c_a0bcb687a2a521ee4b8f96671baa7f1f1}{hMotors}})\ \{}
\DoxyCodeLine{\Hypertarget{driver__Motor_8c_source_l00111}00111\ \ \ \ \ \mbox{\hyperlink{main_8c_a0bcb687a2a521ee4b8f96671baa7f1f1}{hMotors}}-\/>\mbox{\hyperlink{structh__Motor__t_aacedbdb8cb4d02b7279b79c3c82c3bb1}{mode\_mot1}}\ =\ \mbox{\hyperlink{driver__Motor_8h_acf114e04f9a4c659c80ce0106398f85ca6cc2183e0159e2fcbdfd85156b263ec0}{STANDBY\_MODE}};}
\DoxyCodeLine{\Hypertarget{driver__Motor_8c_source_l00112}00112\ \ \ \ \ \mbox{\hyperlink{main_8c_a0bcb687a2a521ee4b8f96671baa7f1f1}{hMotors}}-\/>\mbox{\hyperlink{structh__Motor__t_a40847f19d30aafdc35322769d7849b38}{mode\_mot2}}\ =\ \mbox{\hyperlink{driver__Motor_8h_acf114e04f9a4c659c80ce0106398f85ca6cc2183e0159e2fcbdfd85156b263ec0}{STANDBY\_MODE}};}
\DoxyCodeLine{\Hypertarget{driver__Motor_8c_source_l00113}00113\ \ \ \ \ \mbox{\hyperlink{driver__Motor_8c_a3b02c81c2bf2acaa597535ee656afe16}{Motor\_SetMode}}(\mbox{\hyperlink{main_8c_a0bcb687a2a521ee4b8f96671baa7f1f1}{hMotors}});}
\DoxyCodeLine{\Hypertarget{driver__Motor_8c_source_l00114}00114\ \}}
\DoxyCodeLine{\Hypertarget{driver__Motor_8c_source_l00115}00115\ }
\DoxyCodeLine{\Hypertarget{driver__Motor_8c_source_l00120}\mbox{\hyperlink{driver__Motor_8c_a545aba630910986048b10789d7eefc60}{00120}}\ \textcolor{keywordtype}{void}\ \mbox{\hyperlink{driver__Motor_8c_a545aba630910986048b10789d7eefc60}{Motor\_UpdateSpeed}}(\mbox{\hyperlink{structh__Motor__t}{h\_Motor\_t}}\ *\ \mbox{\hyperlink{main_8c_a0bcb687a2a521ee4b8f96671baa7f1f1}{hMotors}})\ \{}
\DoxyCodeLine{\Hypertarget{driver__Motor_8c_source_l00121}00121\ \ \ \ \ \textcolor{comment}{//\ Increase\ speed\ progressively}}
\DoxyCodeLine{\Hypertarget{driver__Motor_8c_source_l00122}00122\ \ \ \ \ \textcolor{keywordflow}{if}\ (\mbox{\hyperlink{main_8c_a0bcb687a2a521ee4b8f96671baa7f1f1}{hMotors}}-\/>\mbox{\hyperlink{structh__Motor__t_a8df75e44122e148783e198e3e81691ee}{speed1}}\ >\ \mbox{\hyperlink{main_8c_a0bcb687a2a521ee4b8f96671baa7f1f1}{hMotors}}-\/>\mbox{\hyperlink{structh__Motor__t_a14c979980e342e3df7207e6db0df9d76}{current\_speed1}})}
\DoxyCodeLine{\Hypertarget{driver__Motor_8c_source_l00123}00123\ \ \ \ \ \ \ \ \ \mbox{\hyperlink{main_8c_a0bcb687a2a521ee4b8f96671baa7f1f1}{hMotors}}-\/>\mbox{\hyperlink{structh__Motor__t_a14c979980e342e3df7207e6db0df9d76}{current\_speed1}}\ +=\ \mbox{\hyperlink{main_8c_a0bcb687a2a521ee4b8f96671baa7f1f1}{hMotors}}-\/>\mbox{\hyperlink{structh__Motor__t_a5a9eda21d5770e2629c31b5eddbe0dba}{speed\_increase\_rate1}};}
\DoxyCodeLine{\Hypertarget{driver__Motor_8c_source_l00124}00124\ \ \ \ \ \textcolor{keywordflow}{if}\ (\mbox{\hyperlink{main_8c_a0bcb687a2a521ee4b8f96671baa7f1f1}{hMotors}}-\/>\mbox{\hyperlink{structh__Motor__t_ab84050b626016809de350970d5006968}{speed2}}\ >\ \mbox{\hyperlink{main_8c_a0bcb687a2a521ee4b8f96671baa7f1f1}{hMotors}}-\/>\mbox{\hyperlink{structh__Motor__t_a953835017f6e2a80bd10bd5433fa4444}{current\_speed2}})}
\DoxyCodeLine{\Hypertarget{driver__Motor_8c_source_l00125}00125\ \ \ \ \ \ \ \ \ \mbox{\hyperlink{main_8c_a0bcb687a2a521ee4b8f96671baa7f1f1}{hMotors}}-\/>\mbox{\hyperlink{structh__Motor__t_a953835017f6e2a80bd10bd5433fa4444}{current\_speed2}}\ +=\ \mbox{\hyperlink{main_8c_a0bcb687a2a521ee4b8f96671baa7f1f1}{hMotors}}-\/>\mbox{\hyperlink{structh__Motor__t_a3a2ab33027bcc09292944cceea755590}{speed\_increase\_rate2}};}
\DoxyCodeLine{\Hypertarget{driver__Motor_8c_source_l00126}00126\ }
\DoxyCodeLine{\Hypertarget{driver__Motor_8c_source_l00127}00127\ \ \ \ \ \textcolor{comment}{//\ Decrease\ speed\ progressively}}
\DoxyCodeLine{\Hypertarget{driver__Motor_8c_source_l00128}00128\ \ \ \ \ \textcolor{keywordflow}{if}\ (\mbox{\hyperlink{main_8c_a0bcb687a2a521ee4b8f96671baa7f1f1}{hMotors}}-\/>\mbox{\hyperlink{structh__Motor__t_a8df75e44122e148783e198e3e81691ee}{speed1}}\ <\ \mbox{\hyperlink{main_8c_a0bcb687a2a521ee4b8f96671baa7f1f1}{hMotors}}-\/>\mbox{\hyperlink{structh__Motor__t_a14c979980e342e3df7207e6db0df9d76}{current\_speed1}})}
\DoxyCodeLine{\Hypertarget{driver__Motor_8c_source_l00129}00129\ \ \ \ \ \ \ \ \ \mbox{\hyperlink{main_8c_a0bcb687a2a521ee4b8f96671baa7f1f1}{hMotors}}-\/>\mbox{\hyperlink{structh__Motor__t_a14c979980e342e3df7207e6db0df9d76}{current\_speed1}}\ -\/=\ \mbox{\hyperlink{main_8c_a0bcb687a2a521ee4b8f96671baa7f1f1}{hMotors}}-\/>\mbox{\hyperlink{structh__Motor__t_a5a9eda21d5770e2629c31b5eddbe0dba}{speed\_increase\_rate1}};}
\DoxyCodeLine{\Hypertarget{driver__Motor_8c_source_l00130}00130\ \ \ \ \ \textcolor{keywordflow}{if}\ (\mbox{\hyperlink{main_8c_a0bcb687a2a521ee4b8f96671baa7f1f1}{hMotors}}-\/>\mbox{\hyperlink{structh__Motor__t_ab84050b626016809de350970d5006968}{speed2}}\ <\ \mbox{\hyperlink{main_8c_a0bcb687a2a521ee4b8f96671baa7f1f1}{hMotors}}-\/>\mbox{\hyperlink{structh__Motor__t_a953835017f6e2a80bd10bd5433fa4444}{current\_speed2}})}
\DoxyCodeLine{\Hypertarget{driver__Motor_8c_source_l00131}00131\ \ \ \ \ \ \ \ \ \mbox{\hyperlink{main_8c_a0bcb687a2a521ee4b8f96671baa7f1f1}{hMotors}}-\/>\mbox{\hyperlink{structh__Motor__t_a953835017f6e2a80bd10bd5433fa4444}{current\_speed2}}\ -\/=\ \mbox{\hyperlink{main_8c_a0bcb687a2a521ee4b8f96671baa7f1f1}{hMotors}}-\/>\mbox{\hyperlink{structh__Motor__t_a3a2ab33027bcc09292944cceea755590}{speed\_increase\_rate2}};}
\DoxyCodeLine{\Hypertarget{driver__Motor_8c_source_l00132}00132\ }
\DoxyCodeLine{\Hypertarget{driver__Motor_8c_source_l00133}00133\ \ \ \ \ \_\_HAL\_TIM\_SET\_COMPARE(\mbox{\hyperlink{main_8c_a0bcb687a2a521ee4b8f96671baa7f1f1}{hMotors}}-\/>\mbox{\hyperlink{structh__Motor__t_a5dc7d1c65997ccaed48a93a3f4ffc486}{htim}},\ TIM\_CHANNEL\_1,\ \mbox{\hyperlink{main_8c_a0bcb687a2a521ee4b8f96671baa7f1f1}{hMotors}}-\/>\mbox{\hyperlink{structh__Motor__t_a14c979980e342e3df7207e6db0df9d76}{current\_speed1}});}
\DoxyCodeLine{\Hypertarget{driver__Motor_8c_source_l00134}00134\ \ \ \ \ \_\_HAL\_TIM\_SET\_COMPARE(\mbox{\hyperlink{main_8c_a0bcb687a2a521ee4b8f96671baa7f1f1}{hMotors}}-\/>\mbox{\hyperlink{structh__Motor__t_a5dc7d1c65997ccaed48a93a3f4ffc486}{htim}},\ TIM\_CHANNEL\_2,\ \mbox{\hyperlink{main_8c_a0bcb687a2a521ee4b8f96671baa7f1f1}{hMotors}}-\/>\mbox{\hyperlink{structh__Motor__t_a953835017f6e2a80bd10bd5433fa4444}{current\_speed2}});}
\DoxyCodeLine{\Hypertarget{driver__Motor_8c_source_l00135}00135\ \}}

\end{DoxyCode}

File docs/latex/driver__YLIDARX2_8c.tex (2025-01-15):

\doxysection{/home/oliver/\+Documents/3\+A/2425\+\_\+\+ESE\+\_\+\+Projet\+\_\+\+V-\/\+NOM/\+Projet\+\_\+\+V-\/\+NOM\+\_\+\+STM32/\+Core/drivers/driver\+\_\+\+YLIDARX2.c File Reference}
\hypertarget{driver__YLIDARX2_8c}{}\label{driver__YLIDARX2_8c}\index{/home/oliver/Documents/3A/2425\_ESE\_Projet\_V-\/NOM/Projet\_V-\/NOM\_STM32/Core/drivers/driver\_YLIDARX2.c@{/home/oliver/Documents/3A/2425\_ESE\_Projet\_V-\/NOM/Projet\_V-\/NOM\_STM32/Core/drivers/driver\_YLIDARX2.c}}

Implementation of the YDLIDAR X2 driver.  

{\ttfamily \#include "{}driver\+\_\+\+YLIDARX2.\+h"{}}\newline
{\ttfamily \#include $<$string.\+h$>$}\newline
{\ttfamily \#include $<$stdio.\+h$>$}\newline
Include dependency graph for driver\+\_\+\+YLIDARX2.\+c\+:
% FIG 0
\doxysubsubsection*{Macros}
\begin{DoxyCompactItemize}
\item 
\#define \mbox{\hyperlink{driver__YLIDARX2_8c_ad72dbcf6d0153db1b8d8a58001feed83}{DEBUG}}~1
\item 
\#define \mbox{\hyperlink{driver__YLIDARX2_8c_a88edd2aa4feabff4af21a997d5d8aa23}{DEBUG\+\_\+\+PRINT}}(...)~printf(\+\_\+\+\_\+\+VA\+\_\+\+ARGS\+\_\+\+\_\+)
\end{DoxyCompactItemize}
\doxysubsubsection*{Functions}
\begin{DoxyCompactItemize}
\item 
void \mbox{\hyperlink{driver__YLIDARX2_8c_a763cead40ecca92b7b3416d894686709}{YLIDARX2\+\_\+\+Init\+DMA}} (\mbox{\hyperlink{structh__YLIDARX2__t}{h\+\_\+\+YLIDARX2\+\_\+t}} \texorpdfstring{$\ast$}{*}lidar, UART\+\_\+\+Handle\+Type\+Def \texorpdfstring{$\ast$}{*}huart)
\begin{DoxyCompactList}\small\item\em Initialize the YDLIDAR X2 driver with DMA. \end{DoxyCompactList}\item 
void \mbox{\hyperlink{driver__YLIDARX2_8c_a242f78691663fad7e5b74671a38b8942}{YLIDARX2\+\_\+\+Restart\+DMA}} (\mbox{\hyperlink{structh__YLIDARX2__t}{h\+\_\+\+YLIDARX2\+\_\+t}} \texorpdfstring{$\ast$}{*}lidar)
\item 
void \mbox{\hyperlink{driver__YLIDARX2_8c_a93def8b27b98e3f7c450d1ac3bbd45a9}{YLIDARX2\+\_\+\+Process\+DMAHalf\+Complete}} (\mbox{\hyperlink{structh__YLIDARX2__t}{h\+\_\+\+YLIDARX2\+\_\+t}} \texorpdfstring{$\ast$}{*}lidar)
\begin{DoxyCompactList}\small\item\em Process the first half of the DMA buffer. \end{DoxyCompactList}\item 
void \mbox{\hyperlink{driver__YLIDARX2_8c_a849a62d7f79669b165d9a8aa50796b25}{YLIDARX2\+\_\+\+Process\+DMAComplete}} (\mbox{\hyperlink{structh__YLIDARX2__t}{h\+\_\+\+YLIDARX2\+\_\+t}} \texorpdfstring{$\ast$}{*}lidar)
\begin{DoxyCompactList}\small\item\em Process the second half of the DMA buffer. \end{DoxyCompactList}\item 
void \mbox{\hyperlink{driver__YLIDARX2_8c_a80962194ceb6d474ed1dbb0db25032f2}{YLIDARX2\+\_\+\+Process\+Buffer}} (\mbox{\hyperlink{structh__YLIDARX2__t}{h\+\_\+\+YLIDARX2\+\_\+t}} \texorpdfstring{$\ast$}{*}lidar, uint16\+\_\+t start, uint16\+\_\+t end)
\begin{DoxyCompactList}\small\item\em Process a portion of the DMA buffer. \end{DoxyCompactList}\end{DoxyCompactItemize}

\doxysubsection{Detailed Description}
Implementation of the YDLIDAR X2 driver. 

Handles initialization, data reception via DMA, and processing of LIDAR frames.

\begin{DoxyDate}{Date}
Jan 3, 2025 
\end{DoxyDate}
\begin{DoxyAuthor}{Author}
Oliver 
\end{DoxyAuthor}

Definition in file \mbox{\hyperlink{driver__YLIDARX2_8c_source}{driver\+\_\+\+YLIDARX2.\+c}}.

\doxysubsection{Macro Definition Documentation}
\Hypertarget{driver__YLIDARX2_8c_ad72dbcf6d0153db1b8d8a58001feed83}\label{driver__YLIDARX2_8c_ad72dbcf6d0153db1b8d8a58001feed83} 
\index{driver\_YLIDARX2.c@{driver\_YLIDARX2.c}!DEBUG@{DEBUG}}
\index{DEBUG@{DEBUG}!driver\_YLIDARX2.c@{driver\_YLIDARX2.c}}
\doxysubsubsection{\texorpdfstring{DEBUG}{DEBUG}}
{\footnotesize\ttfamily \#define DEBUG~1}

Enable or disable debug logs 

Definition at line \mbox{\hyperlink{driver__YLIDARX2_8c_source_l00016}{16}} of file \mbox{\hyperlink{driver__YLIDARX2_8c_source}{driver\+\_\+\+YLIDARX2.\+c}}.

\Hypertarget{driver__YLIDARX2_8c_a88edd2aa4feabff4af21a997d5d8aa23}\label{driver__YLIDARX2_8c_a88edd2aa4feabff4af21a997d5d8aa23} 
\index{driver\_YLIDARX2.c@{driver\_YLIDARX2.c}!DEBUG\_PRINT@{DEBUG\_PRINT}}
\index{DEBUG\_PRINT@{DEBUG\_PRINT}!driver\_YLIDARX2.c@{driver\_YLIDARX2.c}}
\doxysubsubsection{\texorpdfstring{DEBUG\_PRINT}{DEBUG\_PRINT}}
{\footnotesize\ttfamily \#define DEBUG\+\_\+\+PRINT(\begin{DoxyParamCaption}\item[{}]{... }\end{DoxyParamCaption})~printf(\+\_\+\+\_\+\+VA\+\_\+\+ARGS\+\_\+\+\_\+)}

Definition at line \mbox{\hyperlink{driver__YLIDARX2_8c_source_l00019}{19}} of file \mbox{\hyperlink{driver__YLIDARX2_8c_source}{driver\+\_\+\+YLIDARX2.\+c}}.

\doxysubsection{Function Documentation}
\Hypertarget{driver__YLIDARX2_8c_a763cead40ecca92b7b3416d894686709}\label{driver__YLIDARX2_8c_a763cead40ecca92b7b3416d894686709} 
\index{driver\_YLIDARX2.c@{driver\_YLIDARX2.c}!YLIDARX2\_InitDMA@{YLIDARX2\_InitDMA}}
\index{YLIDARX2\_InitDMA@{YLIDARX2\_InitDMA}!driver\_YLIDARX2.c@{driver\_YLIDARX2.c}}
\doxysubsubsection{\texorpdfstring{YLIDARX2\_InitDMA()}{YLIDARX2\_InitDMA()}}
{\footnotesize\ttfamily void YLIDARX2\+\_\+\+Init\+DMA (\begin{DoxyParamCaption}\item[{\mbox{\hyperlink{structh__YLIDARX2__t}{h\+\_\+\+YLIDARX2\+\_\+t}} \texorpdfstring{$\ast$}{*}}]{lidar,  }\item[{UART\+\_\+\+Handle\+Type\+Def \texorpdfstring{$\ast$}{*}}]{huart }\end{DoxyParamCaption})}

Initialize the YDLIDAR X2 driver with DMA. 

\begin{DoxyParams}{Parameters}
{\em lidar} & Pointer to the YDLIDARX2\+\_\+t structure. \\
\hline
{\em huart} & UART handle for communication. \\
\hline
\end{DoxyParams}

Definition at line \mbox{\hyperlink{driver__YLIDARX2_8c_source_l00034}{34}} of file \mbox{\hyperlink{driver__YLIDARX2_8c_source}{driver\+\_\+\+YLIDARX2.\+c}}.

Here is the caller graph for this function\+:
% FIG 1
\Hypertarget{driver__YLIDARX2_8c_a80962194ceb6d474ed1dbb0db25032f2}\label{driver__YLIDARX2_8c_a80962194ceb6d474ed1dbb0db25032f2} 
\index{driver\_YLIDARX2.c@{driver\_YLIDARX2.c}!YLIDARX2\_ProcessBuffer@{YLIDARX2\_ProcessBuffer}}
\index{YLIDARX2\_ProcessBuffer@{YLIDARX2\_ProcessBuffer}!driver\_YLIDARX2.c@{driver\_YLIDARX2.c}}
\doxysubsubsection{\texorpdfstring{YLIDARX2\_ProcessBuffer()}{YLIDARX2\_ProcessBuffer()}}
{\footnotesize\ttfamily void YLIDARX2\+\_\+\+Process\+Buffer (\begin{DoxyParamCaption}\item[{\mbox{\hyperlink{structh__YLIDARX2__t}{h\+\_\+\+YLIDARX2\+\_\+t}} \texorpdfstring{$\ast$}{*}}]{lidar,  }\item[{uint16\+\_\+t}]{start,  }\item[{uint16\+\_\+t}]{end }\end{DoxyParamCaption})}

Process a portion of the DMA buffer. 

\begin{DoxyParams}{Parameters}
{\em lidar} & Pointer to the YDLIDARX2\+\_\+t structure. \\
\hline
{\em start} & Start index of the buffer to process. \\
\hline
{\em end} & End index of the buffer to process. \\
\hline
\end{DoxyParams}

Definition at line \mbox{\hyperlink{driver__YLIDARX2_8c_source_l00063}{63}} of file \mbox{\hyperlink{driver__YLIDARX2_8c_source}{driver\+\_\+\+YLIDARX2.\+c}}.

Here is the caller graph for this function\+:
% FIG 2
\Hypertarget{driver__YLIDARX2_8c_a849a62d7f79669b165d9a8aa50796b25}\label{driver__YLIDARX2_8c_a849a62d7f79669b165d9a8aa50796b25} 
\index{driver\_YLIDARX2.c@{driver\_YLIDARX2.c}!YLIDARX2\_ProcessDMAComplete@{YLIDARX2\_ProcessDMAComplete}}
\index{YLIDARX2\_ProcessDMAComplete@{YLIDARX2\_ProcessDMAComplete}!driver\_YLIDARX2.c@{driver\_YLIDARX2.c}}
\doxysubsubsection{\texorpdfstring{YLIDARX2\_ProcessDMAComplete()}{YLIDARX2\_ProcessDMAComplete()}}
{\footnotesize\ttfamily void YLIDARX2\+\_\+\+Process\+DMAComplete (\begin{DoxyParamCaption}\item[{\mbox{\hyperlink{structh__YLIDARX2__t}{h\+\_\+\+YLIDARX2\+\_\+t}} \texorpdfstring{$\ast$}{*}}]{lidar }\end{DoxyParamCaption})}

Process the second half of the DMA buffer. 

\begin{DoxyParams}{Parameters}
{\em lidar} & Pointer to the YDLIDARX2\+\_\+t structure. \\
\hline
\end{DoxyParams}

Definition at line \mbox{\hyperlink{driver__YLIDARX2_8c_source_l00059}{59}} of file \mbox{\hyperlink{driver__YLIDARX2_8c_source}{driver\+\_\+\+YLIDARX2.\+c}}.

Here is the call graph for this function\+:
% FIG 3
Here is the caller graph for this function\+:
% FIG 4
\Hypertarget{driver__YLIDARX2_8c_a93def8b27b98e3f7c450d1ac3bbd45a9}\label{driver__YLIDARX2_8c_a93def8b27b98e3f7c450d1ac3bbd45a9} 
\index{driver\_YLIDARX2.c@{driver\_YLIDARX2.c}!YLIDARX2\_ProcessDMAHalfComplete@{YLIDARX2\_ProcessDMAHalfComplete}}
\index{YLIDARX2\_ProcessDMAHalfComplete@{YLIDARX2\_ProcessDMAHalfComplete}!driver\_YLIDARX2.c@{driver\_YLIDARX2.c}}
\doxysubsubsection{\texorpdfstring{YLIDARX2\_ProcessDMAHalfComplete()}{YLIDARX2\_ProcessDMAHalfComplete()}}
{\footnotesize\ttfamily void YLIDARX2\+\_\+\+Process\+DMAHalf\+Complete (\begin{DoxyParamCaption}\item[{\mbox{\hyperlink{structh__YLIDARX2__t}{h\+\_\+\+YLIDARX2\+\_\+t}} \texorpdfstring{$\ast$}{*}}]{lidar }\end{DoxyParamCaption})}

Process the first half of the DMA buffer. 

\begin{DoxyParams}{Parameters}
{\em lidar} & Pointer to the YDLIDARX2\+\_\+t structure. \\
\hline
\end{DoxyParams}

Definition at line \mbox{\hyperlink{driver__YLIDARX2_8c_source_l00055}{55}} of file \mbox{\hyperlink{driver__YLIDARX2_8c_source}{driver\+\_\+\+YLIDARX2.\+c}}.

Here is the call graph for this function\+:
% FIG 5
Here is the caller graph for this function\+:
% FIG 6
\Hypertarget{driver__YLIDARX2_8c_a242f78691663fad7e5b74671a38b8942}\label{driver__YLIDARX2_8c_a242f78691663fad7e5b74671a38b8942} 
\index{driver\_YLIDARX2.c@{driver\_YLIDARX2.c}!YLIDARX2\_RestartDMA@{YLIDARX2\_RestartDMA}}
\index{YLIDARX2\_RestartDMA@{YLIDARX2\_RestartDMA}!driver\_YLIDARX2.c@{driver\_YLIDARX2.c}}
\doxysubsubsection{\texorpdfstring{YLIDARX2\_RestartDMA()}{YLIDARX2\_RestartDMA()}}
{\footnotesize\ttfamily void YLIDARX2\+\_\+\+Restart\+DMA (\begin{DoxyParamCaption}\item[{\mbox{\hyperlink{structh__YLIDARX2__t}{h\+\_\+\+YLIDARX2\+\_\+t}} \texorpdfstring{$\ast$}{*}}]{lidar }\end{DoxyParamCaption})}

Definition at line \mbox{\hyperlink{driver__YLIDARX2_8c_source_l00046}{46}} of file \mbox{\hyperlink{driver__YLIDARX2_8c_source}{driver\+\_\+\+YLIDARX2.\+c}}.

Here is the call graph for this function\+:
% FIG 7

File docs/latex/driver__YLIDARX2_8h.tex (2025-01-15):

\doxysection{/home/oliver/\+Documents/3\+A/2425\+\_\+\+ESE\+\_\+\+Projet\+\_\+\+V-\/\+NOM/\+Projet\+\_\+\+V-\/\+NOM\+\_\+\+STM32/\+Core/drivers/driver\+\_\+\+YLIDARX2.h File Reference}
\hypertarget{driver__YLIDARX2_8h}{}\label{driver__YLIDARX2_8h}\index{/home/oliver/Documents/3A/2425\_ESE\_Projet\_V-\/NOM/Projet\_V-\/NOM\_STM32/Core/drivers/driver\_YLIDARX2.h@{/home/oliver/Documents/3A/2425\_ESE\_Projet\_V-\/NOM/Projet\_V-\/NOM\_STM32/Core/drivers/driver\_YLIDARX2.h}}

Header file for the YDLIDAR X2 driver.  

{\ttfamily \#include "{}usart.\+h"{}}\newline
{\ttfamily \#include $<$stdint.\+h$>$}\newline
{\ttfamily \#include $<$stdbool.\+h$>$}\newline
Include dependency graph for driver\+\_\+\+YLIDARX2.\+h\+:
% FIG 0
This graph shows which files directly or indirectly include this file\+:
% FIG 1
\doxysubsubsection*{Data Structures}
\begin{DoxyCompactItemize}
\item 
struct \mbox{\hyperlink{structYLIDARX2__Point__t}{YLIDARX2\+\_\+\+Point\+\_\+t}}
\begin{DoxyCompactList}\small\item\em Structure to hold individual LIDAR point data. \end{DoxyCompactList}\item 
struct \mbox{\hyperlink{structh__YLIDARX2__t}{h\+\_\+\+YLIDARX2\+\_\+t}}
\begin{DoxyCompactList}\small\item\em Structure to hold LIDAR state and data. \end{DoxyCompactList}\end{DoxyCompactItemize}
\doxysubsubsection*{Macros}
\begin{DoxyCompactItemize}
\item 
\#define \mbox{\hyperlink{driver__YLIDARX2_8h_a9b08f201880f08d1b268f723b138bca0}{YLIDARX2\+\_\+\+DMA\+\_\+\+BUFFER\+\_\+\+SIZE}}~1000
\item 
\#define \mbox{\hyperlink{driver__YLIDARX2_8h_a2baf69d5741479065f9e385ccd2faf8f}{YLIDARX2\+\_\+\+MAX\+\_\+\+POINTS}}~500
\item 
\#define \mbox{\hyperlink{driver__YLIDARX2_8h_a1aa8b6627486da5c445e6bdbe5c2ed0b}{PACKET\+\_\+\+HEADER}}~0x55\+AA
\item 
\#define \mbox{\hyperlink{driver__YLIDARX2_8h_afee58d787f4e5ebb6de7d7eec1621d14}{FRAME\+\_\+\+LENGTH\+\_\+\+MIN}}~7
\end{DoxyCompactItemize}
\doxysubsubsection*{Functions}
\begin{DoxyCompactItemize}
\item 
void \mbox{\hyperlink{driver__YLIDARX2_8h_a763cead40ecca92b7b3416d894686709}{YLIDARX2\+\_\+\+Init\+DMA}} (\mbox{\hyperlink{structh__YLIDARX2__t}{h\+\_\+\+YLIDARX2\+\_\+t}} \texorpdfstring{$\ast$}{*}lidar, UART\+\_\+\+Handle\+Type\+Def \texorpdfstring{$\ast$}{*}huart)
\begin{DoxyCompactList}\small\item\em Initialize the YDLIDAR X2 driver with DMA. \end{DoxyCompactList}\item 
void \mbox{\hyperlink{driver__YLIDARX2_8h_a242f78691663fad7e5b74671a38b8942}{YLIDARX2\+\_\+\+Restart\+DMA}} (\mbox{\hyperlink{structh__YLIDARX2__t}{h\+\_\+\+YLIDARX2\+\_\+t}} \texorpdfstring{$\ast$}{*}lidar)
\item 
void \mbox{\hyperlink{driver__YLIDARX2_8h_a93def8b27b98e3f7c450d1ac3bbd45a9}{YLIDARX2\+\_\+\+Process\+DMAHalf\+Complete}} (\mbox{\hyperlink{structh__YLIDARX2__t}{h\+\_\+\+YLIDARX2\+\_\+t}} \texorpdfstring{$\ast$}{*}lidar)
\begin{DoxyCompactList}\small\item\em Process the first half of the DMA buffer. \end{DoxyCompactList}\item 
void \mbox{\hyperlink{driver__YLIDARX2_8h_a849a62d7f79669b165d9a8aa50796b25}{YLIDARX2\+\_\+\+Process\+DMAComplete}} (\mbox{\hyperlink{structh__YLIDARX2__t}{h\+\_\+\+YLIDARX2\+\_\+t}} \texorpdfstring{$\ast$}{*}lidar)
\begin{DoxyCompactList}\small\item\em Process the second half of the DMA buffer. \end{DoxyCompactList}\item 
void \mbox{\hyperlink{driver__YLIDARX2_8h_a80962194ceb6d474ed1dbb0db25032f2}{YLIDARX2\+\_\+\+Process\+Buffer}} (\mbox{\hyperlink{structh__YLIDARX2__t}{h\+\_\+\+YLIDARX2\+\_\+t}} \texorpdfstring{$\ast$}{*}lidar, uint16\+\_\+t start, uint16\+\_\+t end)
\begin{DoxyCompactList}\small\item\em Process a portion of the DMA buffer. \end{DoxyCompactList}\item 
bool \mbox{\hyperlink{driver__YLIDARX2_8h_aae3a4bf21daa29e6d19c8b209bda693a}{YLIDARX2\+\_\+\+Validate\+Checksum}} (const uint8\+\_\+t \texorpdfstring{$\ast$}{*}data, uint16\+\_\+t length)
\begin{DoxyCompactList}\small\item\em Validate the checksum of a LIDAR frame. \end{DoxyCompactList}\item 
void \mbox{\hyperlink{driver__YLIDARX2_8h_a1428d8ff5ef4c6e4d90fe31050fa59cc}{YLIDARX2\+\_\+\+Process\+Frame}} (\mbox{\hyperlink{structh__YLIDARX2__t}{h\+\_\+\+YLIDARX2\+\_\+t}} \texorpdfstring{$\ast$}{*}lidar, const uint8\+\_\+t \texorpdfstring{$\ast$}{*}frame)
\begin{DoxyCompactList}\small\item\em Process a single LIDAR frame. \end{DoxyCompactList}\end{DoxyCompactItemize}

\doxysubsection{Detailed Description}
Header file for the YDLIDAR X2 driver. 

Provides definitions and function prototypes for initializing, processing, and handling YDLIDAR X2 data using DMA.

\begin{DoxyDate}{Date}
Jan 3, 2025 
\end{DoxyDate}
\begin{DoxyAuthor}{Author}
Oliver 
\end{DoxyAuthor}

Definition in file \mbox{\hyperlink{driver__YLIDARX2_8h_source}{driver\+\_\+\+YLIDARX2.\+h}}.

\doxysubsection{Macro Definition Documentation}
\Hypertarget{driver__YLIDARX2_8h_afee58d787f4e5ebb6de7d7eec1621d14}\label{driver__YLIDARX2_8h_afee58d787f4e5ebb6de7d7eec1621d14} 
\index{driver\_YLIDARX2.h@{driver\_YLIDARX2.h}!FRAME\_LENGTH\_MIN@{FRAME\_LENGTH\_MIN}}
\index{FRAME\_LENGTH\_MIN@{FRAME\_LENGTH\_MIN}!driver\_YLIDARX2.h@{driver\_YLIDARX2.h}}
\doxysubsubsection{\texorpdfstring{FRAME\_LENGTH\_MIN}{FRAME\_LENGTH\_MIN}}
{\footnotesize\ttfamily \#define FRAME\+\_\+\+LENGTH\+\_\+\+MIN~7}

Minimum frame length in bytes 

Definition at line \mbox{\hyperlink{driver__YLIDARX2_8h_source_l00022}{22}} of file \mbox{\hyperlink{driver__YLIDARX2_8h_source}{driver\+\_\+\+YLIDARX2.\+h}}.

\Hypertarget{driver__YLIDARX2_8h_a1aa8b6627486da5c445e6bdbe5c2ed0b}\label{driver__YLIDARX2_8h_a1aa8b6627486da5c445e6bdbe5c2ed0b} 
\index{driver\_YLIDARX2.h@{driver\_YLIDARX2.h}!PACKET\_HEADER@{PACKET\_HEADER}}
\index{PACKET\_HEADER@{PACKET\_HEADER}!driver\_YLIDARX2.h@{driver\_YLIDARX2.h}}
\doxysubsubsection{\texorpdfstring{PACKET\_HEADER}{PACKET\_HEADER}}
{\footnotesize\ttfamily \#define PACKET\+\_\+\+HEADER~0x55\+AA}

Frame header identifier 

Definition at line \mbox{\hyperlink{driver__YLIDARX2_8h_source_l00021}{21}} of file \mbox{\hyperlink{driver__YLIDARX2_8h_source}{driver\+\_\+\+YLIDARX2.\+h}}.

\Hypertarget{driver__YLIDARX2_8h_a9b08f201880f08d1b268f723b138bca0}\label{driver__YLIDARX2_8h_a9b08f201880f08d1b268f723b138bca0} 
\index{driver\_YLIDARX2.h@{driver\_YLIDARX2.h}!YLIDARX2\_DMA\_BUFFER\_SIZE@{YLIDARX2\_DMA\_BUFFER\_SIZE}}
\index{YLIDARX2\_DMA\_BUFFER\_SIZE@{YLIDARX2\_DMA\_BUFFER\_SIZE}!driver\_YLIDARX2.h@{driver\_YLIDARX2.h}}
\doxysubsubsection{\texorpdfstring{YLIDARX2\_DMA\_BUFFER\_SIZE}{YLIDARX2\_DMA\_BUFFER\_SIZE}}
{\footnotesize\ttfamily \#define YLIDARX2\+\_\+\+DMA\+\_\+\+BUFFER\+\_\+\+SIZE~1000}

DMA buffer size for UART reception 

Definition at line \mbox{\hyperlink{driver__YLIDARX2_8h_source_l00019}{19}} of file \mbox{\hyperlink{driver__YLIDARX2_8h_source}{driver\+\_\+\+YLIDARX2.\+h}}.

\Hypertarget{driver__YLIDARX2_8h_a2baf69d5741479065f9e385ccd2faf8f}\label{driver__YLIDARX2_8h_a2baf69d5741479065f9e385ccd2faf8f} 
\index{driver\_YLIDARX2.h@{driver\_YLIDARX2.h}!YLIDARX2\_MAX\_POINTS@{YLIDARX2\_MAX\_POINTS}}
\index{YLIDARX2\_MAX\_POINTS@{YLIDARX2\_MAX\_POINTS}!driver\_YLIDARX2.h@{driver\_YLIDARX2.h}}
\doxysubsubsection{\texorpdfstring{YLIDARX2\_MAX\_POINTS}{YLIDARX2\_MAX\_POINTS}}
{\footnotesize\ttfamily \#define YLIDARX2\+\_\+\+MAX\+\_\+\+POINTS~500}

Maximum number of processed points stored 

Definition at line \mbox{\hyperlink{driver__YLIDARX2_8h_source_l00020}{20}} of file \mbox{\hyperlink{driver__YLIDARX2_8h_source}{driver\+\_\+\+YLIDARX2.\+h}}.

\doxysubsection{Function Documentation}
\Hypertarget{driver__YLIDARX2_8h_a763cead40ecca92b7b3416d894686709}\label{driver__YLIDARX2_8h_a763cead40ecca92b7b3416d894686709} 
\index{driver\_YLIDARX2.h@{driver\_YLIDARX2.h}!YLIDARX2\_InitDMA@{YLIDARX2\_InitDMA}}
\index{YLIDARX2\_InitDMA@{YLIDARX2\_InitDMA}!driver\_YLIDARX2.h@{driver\_YLIDARX2.h}}
\doxysubsubsection{\texorpdfstring{YLIDARX2\_InitDMA()}{YLIDARX2\_InitDMA()}}
{\footnotesize\ttfamily void YLIDARX2\+\_\+\+Init\+DMA (\begin{DoxyParamCaption}\item[{\mbox{\hyperlink{structh__YLIDARX2__t}{h\+\_\+\+YLIDARX2\+\_\+t}} \texorpdfstring{$\ast$}{*}}]{lidar,  }\item[{UART\+\_\+\+Handle\+Type\+Def \texorpdfstring{$\ast$}{*}}]{huart }\end{DoxyParamCaption})}

Initialize the YDLIDAR X2 driver with DMA. 

\begin{DoxyParams}{Parameters}
{\em lidar} & Pointer to the YDLIDARX2\+\_\+t structure. \\
\hline
{\em huart} & UART handle for communication. \\
\hline
\end{DoxyParams}

Definition at line \mbox{\hyperlink{driver__YLIDARX2_8c_source_l00034}{34}} of file \mbox{\hyperlink{driver__YLIDARX2_8c_source}{driver\+\_\+\+YLIDARX2.\+c}}.

Here is the caller graph for this function\+:
% FIG 2
\Hypertarget{driver__YLIDARX2_8h_a80962194ceb6d474ed1dbb0db25032f2}\label{driver__YLIDARX2_8h_a80962194ceb6d474ed1dbb0db25032f2} 
\index{driver\_YLIDARX2.h@{driver\_YLIDARX2.h}!YLIDARX2\_ProcessBuffer@{YLIDARX2\_ProcessBuffer}}
\index{YLIDARX2\_ProcessBuffer@{YLIDARX2\_ProcessBuffer}!driver\_YLIDARX2.h@{driver\_YLIDARX2.h}}
\doxysubsubsection{\texorpdfstring{YLIDARX2\_ProcessBuffer()}{YLIDARX2\_ProcessBuffer()}}
{\footnotesize\ttfamily void YLIDARX2\+\_\+\+Process\+Buffer (\begin{DoxyParamCaption}\item[{\mbox{\hyperlink{structh__YLIDARX2__t}{h\+\_\+\+YLIDARX2\+\_\+t}} \texorpdfstring{$\ast$}{*}}]{lidar,  }\item[{uint16\+\_\+t}]{start,  }\item[{uint16\+\_\+t}]{end }\end{DoxyParamCaption})}

Process a portion of the DMA buffer. 

\begin{DoxyParams}{Parameters}
{\em lidar} & Pointer to the YDLIDARX2\+\_\+t structure. \\
\hline
{\em start} & Start index of the buffer to process. \\
\hline
{\em end} & End index of the buffer to process. \\
\hline
\end{DoxyParams}

Definition at line \mbox{\hyperlink{driver__YLIDARX2_8c_source_l00063}{63}} of file \mbox{\hyperlink{driver__YLIDARX2_8c_source}{driver\+\_\+\+YLIDARX2.\+c}}.

Here is the caller graph for this function\+:
% FIG 3
\Hypertarget{driver__YLIDARX2_8h_a849a62d7f79669b165d9a8aa50796b25}\label{driver__YLIDARX2_8h_a849a62d7f79669b165d9a8aa50796b25} 
\index{driver\_YLIDARX2.h@{driver\_YLIDARX2.h}!YLIDARX2\_ProcessDMAComplete@{YLIDARX2\_ProcessDMAComplete}}
\index{YLIDARX2\_ProcessDMAComplete@{YLIDARX2\_ProcessDMAComplete}!driver\_YLIDARX2.h@{driver\_YLIDARX2.h}}
\doxysubsubsection{\texorpdfstring{YLIDARX2\_ProcessDMAComplete()}{YLIDARX2\_ProcessDMAComplete()}}
{\footnotesize\ttfamily void YLIDARX2\+\_\+\+Process\+DMAComplete (\begin{DoxyParamCaption}\item[{\mbox{\hyperlink{structh__YLIDARX2__t}{h\+\_\+\+YLIDARX2\+\_\+t}} \texorpdfstring{$\ast$}{*}}]{lidar }\end{DoxyParamCaption})}

Process the second half of the DMA buffer. 

\begin{DoxyParams}{Parameters}
{\em lidar} & Pointer to the YDLIDARX2\+\_\+t structure. \\
\hline
\end{DoxyParams}

Definition at line \mbox{\hyperlink{driver__YLIDARX2_8c_source_l00059}{59}} of file \mbox{\hyperlink{driver__YLIDARX2_8c_source}{driver\+\_\+\+YLIDARX2.\+c}}.

Here is the call graph for this function\+:
% FIG 4
Here is the caller graph for this function\+:
% FIG 5
\Hypertarget{driver__YLIDARX2_8h_a93def8b27b98e3f7c450d1ac3bbd45a9}\label{driver__YLIDARX2_8h_a93def8b27b98e3f7c450d1ac3bbd45a9} 
\index{driver\_YLIDARX2.h@{driver\_YLIDARX2.h}!YLIDARX2\_ProcessDMAHalfComplete@{YLIDARX2\_ProcessDMAHalfComplete}}
\index{YLIDARX2\_ProcessDMAHalfComplete@{YLIDARX2\_ProcessDMAHalfComplete}!driver\_YLIDARX2.h@{driver\_YLIDARX2.h}}
\doxysubsubsection{\texorpdfstring{YLIDARX2\_ProcessDMAHalfComplete()}{YLIDARX2\_ProcessDMAHalfComplete()}}
{\footnotesize\ttfamily void YLIDARX2\+\_\+\+Process\+DMAHalf\+Complete (\begin{DoxyParamCaption}\item[{\mbox{\hyperlink{structh__YLIDARX2__t}{h\+\_\+\+YLIDARX2\+\_\+t}} \texorpdfstring{$\ast$}{*}}]{lidar }\end{DoxyParamCaption})}

Process the first half of the DMA buffer. 

\begin{DoxyParams}{Parameters}
{\em lidar} & Pointer to the YDLIDARX2\+\_\+t structure. \\
\hline
\end{DoxyParams}

Definition at line \mbox{\hyperlink{driver__YLIDARX2_8c_source_l00055}{55}} of file \mbox{\hyperlink{driver__YLIDARX2_8c_source}{driver\+\_\+\+YLIDARX2.\+c}}.

Here is the call graph for this function\+:
% FIG 6
Here is the caller graph for this function\+:
% FIG 7
\Hypertarget{driver__YLIDARX2_8h_a1428d8ff5ef4c6e4d90fe31050fa59cc}\label{driver__YLIDARX2_8h_a1428d8ff5ef4c6e4d90fe31050fa59cc} 
\index{driver\_YLIDARX2.h@{driver\_YLIDARX2.h}!YLIDARX2\_ProcessFrame@{YLIDARX2\_ProcessFrame}}
\index{YLIDARX2\_ProcessFrame@{YLIDARX2\_ProcessFrame}!driver\_YLIDARX2.h@{driver\_YLIDARX2.h}}
\doxysubsubsection{\texorpdfstring{YLIDARX2\_ProcessFrame()}{YLIDARX2\_ProcessFrame()}}
{\footnotesize\ttfamily void YLIDARX2\+\_\+\+Process\+Frame (\begin{DoxyParamCaption}\item[{\mbox{\hyperlink{structh__YLIDARX2__t}{h\+\_\+\+YLIDARX2\+\_\+t}} \texorpdfstring{$\ast$}{*}}]{lidar,  }\item[{const uint8\+\_\+t \texorpdfstring{$\ast$}{*}}]{frame }\end{DoxyParamCaption})}

Process a single LIDAR frame. 

Extracts angle, distance, and intensity from the frame.

\begin{DoxyParams}{Parameters}
{\em lidar} & Pointer to the YDLIDARX2\+\_\+t structure. \\
\hline
{\em frame} & Pointer to the frame data. \\
\hline
\end{DoxyParams}
\Hypertarget{driver__YLIDARX2_8h_a242f78691663fad7e5b74671a38b8942}\label{driver__YLIDARX2_8h_a242f78691663fad7e5b74671a38b8942} 
\index{driver\_YLIDARX2.h@{driver\_YLIDARX2.h}!YLIDARX2\_RestartDMA@{YLIDARX2\_RestartDMA}}
\index{YLIDARX2\_RestartDMA@{YLIDARX2\_RestartDMA}!driver\_YLIDARX2.h@{driver\_YLIDARX2.h}}
\doxysubsubsection{\texorpdfstring{YLIDARX2\_RestartDMA()}{YLIDARX2\_RestartDMA()}}
{\footnotesize\ttfamily void YLIDARX2\+\_\+\+Restart\+DMA (\begin{DoxyParamCaption}\item[{\mbox{\hyperlink{structh__YLIDARX2__t}{h\+\_\+\+YLIDARX2\+\_\+t}} \texorpdfstring{$\ast$}{*}}]{lidar }\end{DoxyParamCaption})}

Definition at line \mbox{\hyperlink{driver__YLIDARX2_8c_source_l00046}{46}} of file \mbox{\hyperlink{driver__YLIDARX2_8c_source}{driver\+\_\+\+YLIDARX2.\+c}}.

Here is the call graph for this function\+:
% FIG 8
\Hypertarget{driver__YLIDARX2_8h_aae3a4bf21daa29e6d19c8b209bda693a}\label{driver__YLIDARX2_8h_aae3a4bf21daa29e6d19c8b209bda693a} 
\index{driver\_YLIDARX2.h@{driver\_YLIDARX2.h}!YLIDARX2\_ValidateChecksum@{YLIDARX2\_ValidateChecksum}}
\index{YLIDARX2\_ValidateChecksum@{YLIDARX2\_ValidateChecksum}!driver\_YLIDARX2.h@{driver\_YLIDARX2.h}}
\doxysubsubsection{\texorpdfstring{YLIDARX2\_ValidateChecksum()}{YLIDARX2\_ValidateChecksum()}}
{\footnotesize\ttfamily bool YLIDARX2\+\_\+\+Validate\+Checksum (\begin{DoxyParamCaption}\item[{const uint8\+\_\+t \texorpdfstring{$\ast$}{*}}]{data,  }\item[{uint16\+\_\+t}]{length }\end{DoxyParamCaption})}

Validate the checksum of a LIDAR frame. 

\begin{DoxyParams}{Parameters}
{\em data} & Pointer to the frame data. \\
\hline
{\em length} & Length of the frame. \\
\hline
\end{DoxyParams}
\begin{DoxyReturn}{Returns}
True if the checksum is valid, false otherwise. 
\end{DoxyReturn}

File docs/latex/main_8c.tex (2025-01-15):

\doxysection{/home/oliver/\+Documents/3\+A/2425\+\_\+\+ESE\+\_\+\+Projet\+\_\+\+V-\/\+NOM/\+Projet\+\_\+\+V-\/\+NOM\+\_\+\+STM32/\+Core/\+Src/main.c File Reference}
\hypertarget{main_8c}{}\label{main_8c}\index{/home/oliver/Documents/3A/2425\_ESE\_Projet\_V-\/NOM/Projet\_V-\/NOM\_STM32/Core/Src/main.c@{/home/oliver/Documents/3A/2425\_ESE\_Projet\_V-\/NOM/Projet\_V-\/NOM\_STM32/Core/Src/main.c}}

\+: Main program body  

{\ttfamily \#include "{}main.\+h"{}}\newline
{\ttfamily \#include "{}cmsis\+\_\+os.\+h"{}}\newline
{\ttfamily \#include "{}adc.\+h"{}}\newline
{\ttfamily \#include "{}dma.\+h"{}}\newline
{\ttfamily \#include "{}spi.\+h"{}}\newline
{\ttfamily \#include "{}tim.\+h"{}}\newline
{\ttfamily \#include "{}usart.\+h"{}}\newline
{\ttfamily \#include "{}gpio.\+h"{}}\newline
{\ttfamily \#include $<$stdio.\+h$>$}\newline
{\ttfamily \#include $<$stdlib.\+h$>$}\newline
{\ttfamily \#include "{}stm32g4xx\+\_\+hal.\+h"{}}\newline
{\ttfamily \#include "{}../drivers/driver\+\_\+\+Motor.\+h"{}}\newline
{\ttfamily \#include "{}../drivers/driver\+\_\+\+GP2\+Y0\+A41\+SK0\+F.\+h"{}}\newline
{\ttfamily \#include "{}../drivers/driver\+\_\+\+YLIDARX2.\+h"{}}\newline
{\ttfamily \#include "{}../drivers/driver\+\_\+\+ADXL343.\+h"{}}\newline
Include dependency graph for main.\+c\+:
% FIG 0
\doxysubsubsection*{Macros}
\begin{DoxyCompactItemize}
\item 
\#define \mbox{\hyperlink{main_8c_ad72dbcf6d0153db1b8d8a58001feed83}{DEBUG}}~1
\item 
\#define \mbox{\hyperlink{main_8c_a88edd2aa4feabff4af21a997d5d8aa23}{DEBUG\+\_\+\+PRINT}}(...)~printf(\+\_\+\+\_\+\+VA\+\_\+\+ARGS\+\_\+\+\_\+)
\item 
\#define \mbox{\hyperlink{main_8c_a6423a880df59733d2d9b509c7718d3a9}{STACK\+\_\+\+SIZE}}~256
\item 
\#define \mbox{\hyperlink{main_8c_a91bd5a224ef886a986db440d15be4397}{TASK\+\_\+\+PRIORITY\+\_\+\+MOTOR}}~10
\item 
\#define \mbox{\hyperlink{main_8c_ac5576123162ae1669c3f0d2b0ede59f8}{TASK\+\_\+\+PRIORITY\+\_\+\+CONTROL}}~2
\item 
\#define \mbox{\hyperlink{main_8c_a4126d324f758cfaaddd14dbc048e3441}{TOF\+\_\+\+TRESHHOLD}}~40
\item 
\#define \mbox{\hyperlink{main_8c_ad9f5ab5ce9186dd30e74331b822a3317}{DEBOUNCE\+\_\+\+DELAY\+\_\+\+MS}}~50
\end{DoxyCompactItemize}
\doxysubsubsection*{Functions}
\begin{DoxyCompactItemize}
\item 
void \mbox{\hyperlink{main_8c_a70af21c671abfcc773614a9a4f63d920}{System\+Clock\+\_\+\+Config}} (void)
\begin{DoxyCompactList}\small\item\em System Clock Configuration. \end{DoxyCompactList}\item 
void \mbox{\hyperlink{main_8c_abade755e13d07c10889ae83143656158}{MX\+\_\+\+FREERTOS\+\_\+\+Init}} (void)
\begin{DoxyCompactList}\small\item\em Free\+RTOS initialization. \end{DoxyCompactList}\item 
int \mbox{\hyperlink{main_8c_abc513dd972081ae765b6949a62872eb7}{\+\_\+\+\_\+io\+\_\+putchar}} (int ch)
\begin{DoxyCompactList}\small\item\em Transmit a character over UART. \end{DoxyCompactList}\item 
void \mbox{\hyperlink{main_8c_a1884970cc493d8efba5aec28c0d526e7}{HAL\+\_\+\+UART\+\_\+\+Rx\+Half\+Cplt\+Callback}} (UART\+\_\+\+Handle\+Type\+Def \texorpdfstring{$\ast$}{*}huart)
\begin{DoxyCompactList}\small\item\em Interrupt callbacks. \end{DoxyCompactList}\item 
void \mbox{\hyperlink{main_8c_ae494a9643f29b87d6d81e5264e60e57b}{HAL\+\_\+\+UART\+\_\+\+Rx\+Cplt\+Callback}} (UART\+\_\+\+Handle\+Type\+Def \texorpdfstring{$\ast$}{*}huart)
\begin{DoxyCompactList}\small\item\em UART receive complete callback. \end{DoxyCompactList}\item 
void \mbox{\hyperlink{main_8c_a0cd91fd3a9608559c2a87a8ba6cba55f}{HAL\+\_\+\+GPIO\+\_\+\+EXTI\+\_\+\+Callback}} (uint16\+\_\+t GPIO\+\_\+\+Pin)
\begin{DoxyCompactList}\small\item\em GPIO interrupt callback for EXTI line. \end{DoxyCompactList}\item 
void \mbox{\hyperlink{main_8c_a8f10a863197fb81d232a412773658b78}{task\+\_\+\+Motors}} (void \texorpdfstring{$\ast$}{*}unsused)
\begin{DoxyCompactList}\small\item\em Task declarations. \end{DoxyCompactList}\item 
void \mbox{\hyperlink{main_8c_acd1f91d39bdbd6e86a287e6c0f6eb700}{task\+\_\+\+Control}} (void \texorpdfstring{$\ast$}{*}unsused)
\begin{DoxyCompactList}\small\item\em Behavior control task. \end{DoxyCompactList}\item 
void \mbox{\hyperlink{main_8c_aa78a978fbd2432d86e6dd4b572b368af}{err\+Handler\+\_\+x\+Task\+Create}} (Base\+Type\+\_\+t r)
\begin{DoxyCompactList}\small\item\em Handles errors during task creation. \end{DoxyCompactList}\item 
int \mbox{\hyperlink{main_8c_a840291bc02cba5474a4cb46a9b9566fe}{main}} (void)
\begin{DoxyCompactList}\small\item\em The application entry point. \end{DoxyCompactList}\item 
void \mbox{\hyperlink{main_8c_a0e0456ea96d55db31de947fb3e954f18}{HAL\+\_\+\+UART\+\_\+\+Error\+Callback}} (UART\+\_\+\+Handle\+Type\+Def \texorpdfstring{$\ast$}{*}huart)
\begin{DoxyCompactList}\small\item\em UART error callback. \end{DoxyCompactList}\item 
void \mbox{\hyperlink{main_8c_a8a3b0ad512a6e6c6157440b68d395eac}{HAL\+\_\+\+TIM\+\_\+\+Period\+Elapsed\+Callback}} (TIM\+\_\+\+Handle\+Type\+Def \texorpdfstring{$\ast$}{*}htim)
\begin{DoxyCompactList}\small\item\em Period elapsed callback in non blocking mode. \end{DoxyCompactList}\item 
void \mbox{\hyperlink{main_8c_a1730ffe1e560465665eb47d9264826f9}{Error\+\_\+\+Handler}} (void)
\begin{DoxyCompactList}\small\item\em This function is executed in case of error occurrence. \end{DoxyCompactList}\end{DoxyCompactItemize}
\doxysubsubsection*{Variables}
\begin{DoxyCompactItemize}
\item 
char \mbox{\hyperlink{main_8c_a6756b7138c240d2483fae1eb2ae7cd3a}{small\+\_\+logo\+\_\+msg}} \mbox{[}$\,$\mbox{]}
\item 
char \mbox{\hyperlink{main_8c_ade7bc344359b5fe560adf6d6b5d2e2da}{big\+\_\+logo\+\_\+msg}} \mbox{[}$\,$\mbox{]}
\item 
char \mbox{\hyperlink{main_8c_a11d9c5d5126fbb2339ad812c80f29cac}{jumbo\+\_\+logo\+\_\+msg}} \mbox{[}$\,$\mbox{]}
\item 
\mbox{\hyperlink{structh__YLIDARX2__t}{h\+\_\+\+YLIDARX2\+\_\+t}} \mbox{\hyperlink{main_8c_a493c06babb7cdbc7da75be96c812804f}{hlidar}}
\item 
\mbox{\hyperlink{structh__Motor__t}{h\+\_\+\+Motor\+\_\+t}} \mbox{\hyperlink{main_8c_a0bcb687a2a521ee4b8f96671baa7f1f1}{h\+Motors}}
\item 
\mbox{\hyperlink{structh__GP2Y0A41SK0F__t}{h\+\_\+\+GP2\+Y0\+A41\+SK0\+F\+\_\+t}} \mbox{\hyperlink{main_8c_a9b31bf900b0aef147d175d0d2b6aa78b}{h\+Tof}}
\item 
\mbox{\hyperlink{structh__ADXL343__t}{h\+\_\+\+ADXL343\+\_\+t}} \mbox{\hyperlink{main_8c_a708a0148f469d00ce01b25449488baad}{h\+ADXL}}
\item 
Task\+Handle\+\_\+t \mbox{\hyperlink{main_8c_a8699d330202dcaf5c9a654a7aa93d11c}{x\+Motors}}
\item 
Task\+Handle\+\_\+t \mbox{\hyperlink{main_8c_abad334b01a2fdbe2fb5ce1dff6cd2101}{x\+Control}}
\item 
Semaphore\+Handle\+\_\+t \mbox{\hyperlink{main_8c_ae146f0f510d7944fd0e8ffd727b32f24}{x\+Mutex}}
\item 
volatile uint8\+\_\+t \mbox{\hyperlink{main_8c_a7c1f19ca953a6efd92b19e85dc17a798}{button\+Start\+Pressed}} = 1
\end{DoxyCompactItemize}

\doxysubsection{Detailed Description}
\+: Main program body 

\begin{DoxyAttention}{Attention}

\end{DoxyAttention}
Copyright (c) 2024 STMicroelectronics. All rights reserved.

This software is licensed under terms that can be found in the LICENSE file in the root directory of this software component. If no LICENSE file comes with this software, it is provided AS-\/\+IS. 

Definition in file \mbox{\hyperlink{main_8c_source}{main.\+c}}.

\doxysubsection{Macro Definition Documentation}
\Hypertarget{main_8c_ad9f5ab5ce9186dd30e74331b822a3317}\label{main_8c_ad9f5ab5ce9186dd30e74331b822a3317} 
\index{main.c@{main.c}!DEBOUNCE\_DELAY\_MS@{DEBOUNCE\_DELAY\_MS}}
\index{DEBOUNCE\_DELAY\_MS@{DEBOUNCE\_DELAY\_MS}!main.c@{main.c}}
\doxysubsubsection{\texorpdfstring{DEBOUNCE\_DELAY\_MS}{DEBOUNCE\_DELAY\_MS}}
{\footnotesize\ttfamily \#define DEBOUNCE\+\_\+\+DELAY\+\_\+\+MS~50}

Debounce delay in milliseconds 

Definition at line \mbox{\hyperlink{main_8c_source_l00064}{64}} of file \mbox{\hyperlink{main_8c_source}{main.\+c}}.

\Hypertarget{main_8c_ad72dbcf6d0153db1b8d8a58001feed83}\label{main_8c_ad72dbcf6d0153db1b8d8a58001feed83} 
\index{main.c@{main.c}!DEBUG@{DEBUG}}
\index{DEBUG@{DEBUG}!main.c@{main.c}}
\doxysubsubsection{\texorpdfstring{DEBUG}{DEBUG}}
{\footnotesize\ttfamily \#define DEBUG~1}

Enable or disable debug logs 

Definition at line \mbox{\hyperlink{main_8c_source_l00050}{50}} of file \mbox{\hyperlink{main_8c_source}{main.\+c}}.

\Hypertarget{main_8c_a88edd2aa4feabff4af21a997d5d8aa23}\label{main_8c_a88edd2aa4feabff4af21a997d5d8aa23} 
\index{main.c@{main.c}!DEBUG\_PRINT@{DEBUG\_PRINT}}
\index{DEBUG\_PRINT@{DEBUG\_PRINT}!main.c@{main.c}}
\doxysubsubsection{\texorpdfstring{DEBUG\_PRINT}{DEBUG\_PRINT}}
{\footnotesize\ttfamily \#define DEBUG\+\_\+\+PRINT(\begin{DoxyParamCaption}\item[{}]{... }\end{DoxyParamCaption})~printf(\+\_\+\+\_\+\+VA\+\_\+\+ARGS\+\_\+\+\_\+)}

Definition at line \mbox{\hyperlink{main_8c_source_l00053}{53}} of file \mbox{\hyperlink{main_8c_source}{main.\+c}}.

\Hypertarget{main_8c_a6423a880df59733d2d9b509c7718d3a9}\label{main_8c_a6423a880df59733d2d9b509c7718d3a9} 
\index{main.c@{main.c}!STACK\_SIZE@{STACK\_SIZE}}
\index{STACK\_SIZE@{STACK\_SIZE}!main.c@{main.c}}
\doxysubsubsection{\texorpdfstring{STACK\_SIZE}{STACK\_SIZE}}
{\footnotesize\ttfamily \#define STACK\+\_\+\+SIZE~256}

Definition at line \mbox{\hyperlink{main_8c_source_l00058}{58}} of file \mbox{\hyperlink{main_8c_source}{main.\+c}}.

\Hypertarget{main_8c_ac5576123162ae1669c3f0d2b0ede59f8}\label{main_8c_ac5576123162ae1669c3f0d2b0ede59f8} 
\index{main.c@{main.c}!TASK\_PRIORITY\_CONTROL@{TASK\_PRIORITY\_CONTROL}}
\index{TASK\_PRIORITY\_CONTROL@{TASK\_PRIORITY\_CONTROL}!main.c@{main.c}}
\doxysubsubsection{\texorpdfstring{TASK\_PRIORITY\_CONTROL}{TASK\_PRIORITY\_CONTROL}}
{\footnotesize\ttfamily \#define TASK\+\_\+\+PRIORITY\+\_\+\+CONTROL~2}

Definition at line \mbox{\hyperlink{main_8c_source_l00060}{60}} of file \mbox{\hyperlink{main_8c_source}{main.\+c}}.

\Hypertarget{main_8c_a91bd5a224ef886a986db440d15be4397}\label{main_8c_a91bd5a224ef886a986db440d15be4397} 
\index{main.c@{main.c}!TASK\_PRIORITY\_MOTOR@{TASK\_PRIORITY\_MOTOR}}
\index{TASK\_PRIORITY\_MOTOR@{TASK\_PRIORITY\_MOTOR}!main.c@{main.c}}
\doxysubsubsection{\texorpdfstring{TASK\_PRIORITY\_MOTOR}{TASK\_PRIORITY\_MOTOR}}
{\footnotesize\ttfamily \#define TASK\+\_\+\+PRIORITY\+\_\+\+MOTOR~10}

Definition at line \mbox{\hyperlink{main_8c_source_l00059}{59}} of file \mbox{\hyperlink{main_8c_source}{main.\+c}}.
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

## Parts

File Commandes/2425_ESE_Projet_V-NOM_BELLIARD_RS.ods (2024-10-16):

RS |  |  |  |  | Envoyez un seul fichier par mail!
Pos | I | P | Art | Désignation | Qté commandée | UA | Date Livraison | Prix unitaire | Devise | Q | Grpe | Div
10 | Z |  |  | Capteur ToF 666-6568 | 2 | PC |  | 9.37 | EUR | PC | TA.01
20 | Z |  |  |  |  | PC |  |  | EUR | PC | TA.01
30 | Z |  |  |  |  | PC |  |  | EUR | PC | TA.01
40 | Z |  |  |  |  | PC |  |  | EUR | PC | TA.01
50 | Z |  |  |  |  | PC |  |  | EUR | PC | TA.01
60 | Z |  |  |  |  | PC |  |  | EUR | PC | TA.01
70 | Z |  |  |  |  | PC |  |  | EUR | PC | TA.01
80 | Z |  |  |  |  | PC |  |  | EUR | PC | TA.01
90 | Z |  |  |  |  | PC |  |  | EUR | PC | TA.01
100 | Z |  |  |  |  | PC |  |  | EUR | PC | TA.01
110 | Z |  |  |  |  | PC |  |  | EUR | PC | TA.01
120 | Z |  |  |  |  | PC |  |  | EUR | PC | TA.01
130 | Z |  |  |  |  | PC |  |  | EUR | PC | TA.01
140 | Z |  |  |  |  | PC |  |  | EUR | PC | TA.01
150 | Z |  |  |  |  | PC |  |  | EUR | PC | TA.01
160 | Z |  |  |  |  | PC |  |  | EUR | PC | TA.01
170 | Z |  |  |  |  | PC |  |  | EUR | PC | TA.01
180 | Z |  |  |  |  | PC |  |  | EUR | PC | TA.01
190 | Z |  |  |  |  | PC |  |  | EUR | PC | TA.01
MODE d'EMPLOI et CODE erreurs Version 19
1: indiquez le fournisseur ligne 1
2:remplissez pour chaque ligne commandée les 4 champs en rouge selon les règles suivantes:
 | Art
 |  |  | 2.1 | Ne mettez rien ici tout comme dans P: remplissez les zones rouges (et pas ailleurs)
 | Désignation
 |  |  | 2.2 | Ne dépassez pas les 40 caractères: il seront automatiquement effacés lors de la recopie
 |  |  | 2.3 | Mettre le code commande impérativement en premier suivi d'une courte description
 |  |  | 2.4 | Pour RS et Farnell : mettre le code commande RS ou Farnell (7 à 9 chiffres) (et pas la référence constructeur) suivie d'une courte description
 |  |  | 2.5 | Exemple: 125-4857 capa 1uF 0508
 | Qté commandée
 |  |  | 2.6 | C'est le nombre d'unités correspondant au prix unitaire
 |  |  | 2.7 | Attention il y a des pièges
 |  |  | 2.8 | avec RS par exemple on vous demande parfois de commander par lot de 5 par exemple
 |  |  | 2.9 | si vous commandez 1 lot : le nombre d'unité est alors 5 pour 1 lot et non 1
 | date
 |  |  | 2.10 | Pour la date: mettre la de date dans une semaine
 |  |  | 2.11 | La mettre au format JJ.MM.AAAA
 |  |  | 2.13 | Bien utiliser les points comme séparateur
 | prix unitaire
 |  |  | 2.14 | Le prix est le prix HT (sans la TVA 20%) en euros d'une unité | sauf pour les commandes au comptant ou chez un fournisseur étranger (EXP-TECH par exemple): mettez le prix TTC
 |  |  | 2.15 | arrondi au centime supérieur (0.012 euros devient 0.02!)
 |  |  | 2.16 | avec pour séparateur le point
 |  |  | 2.17 | n'utilisez pas le symbole euros d'excel
3: frais de port
 |  |  | 3.1 | ajoutez une ligne pour les frais de port
 |  |  | 3.2 | dont la désignation est "frais de port"
 |  |  | 3.3 | pas de frais de port à mettre pour RS ou Farnell
 |  |  | 3.4 | Renseignez vous pour connaître les frais de port | 9,9 euros TTC chez EXP par exemple
4: conseils complémentaires
 |  |  | 4.1 | Ne modifier que les 4 champs en rouge
 |  |  | 4.2 | Ne pas modifier le document sinon cela n'a plus aucun intérêt
 |  |  | 4.3 | Mettez les références dans le même ordre que celui de la commande
 |  |  | 4.4 | Vérifier bien sur les sites les références et les prix!
 |  |  | 4.5 | N'oubliez pas les frais de port!: ajoutez une ligne pour les mentionner
5: sauvegardez le fichier au format xls

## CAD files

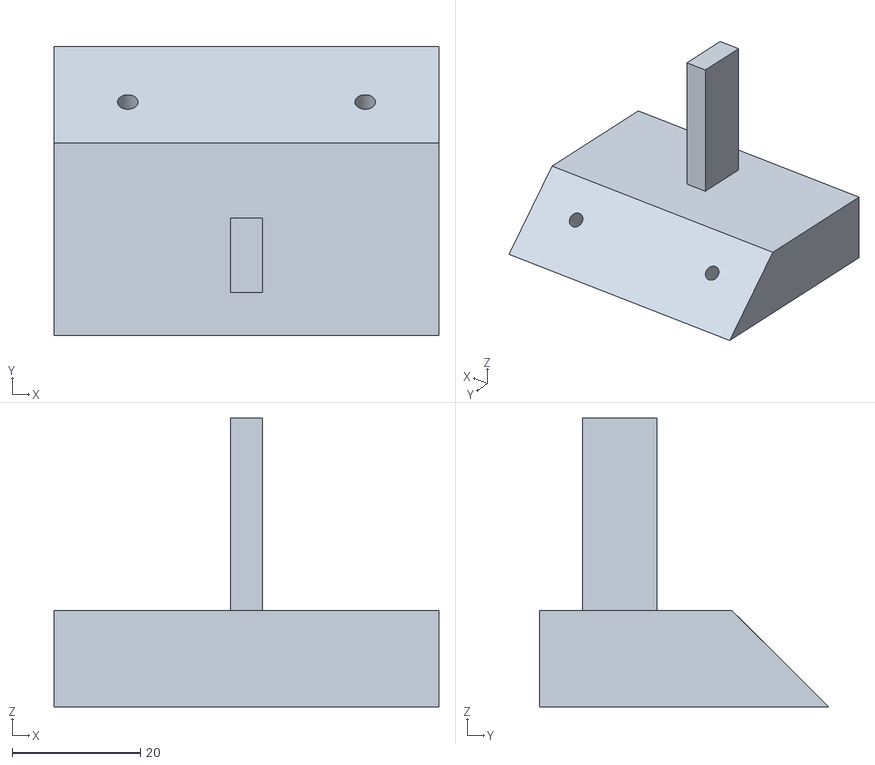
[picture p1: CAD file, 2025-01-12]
Mecanique/support.stl
60.0 x 45.0 x 45.0

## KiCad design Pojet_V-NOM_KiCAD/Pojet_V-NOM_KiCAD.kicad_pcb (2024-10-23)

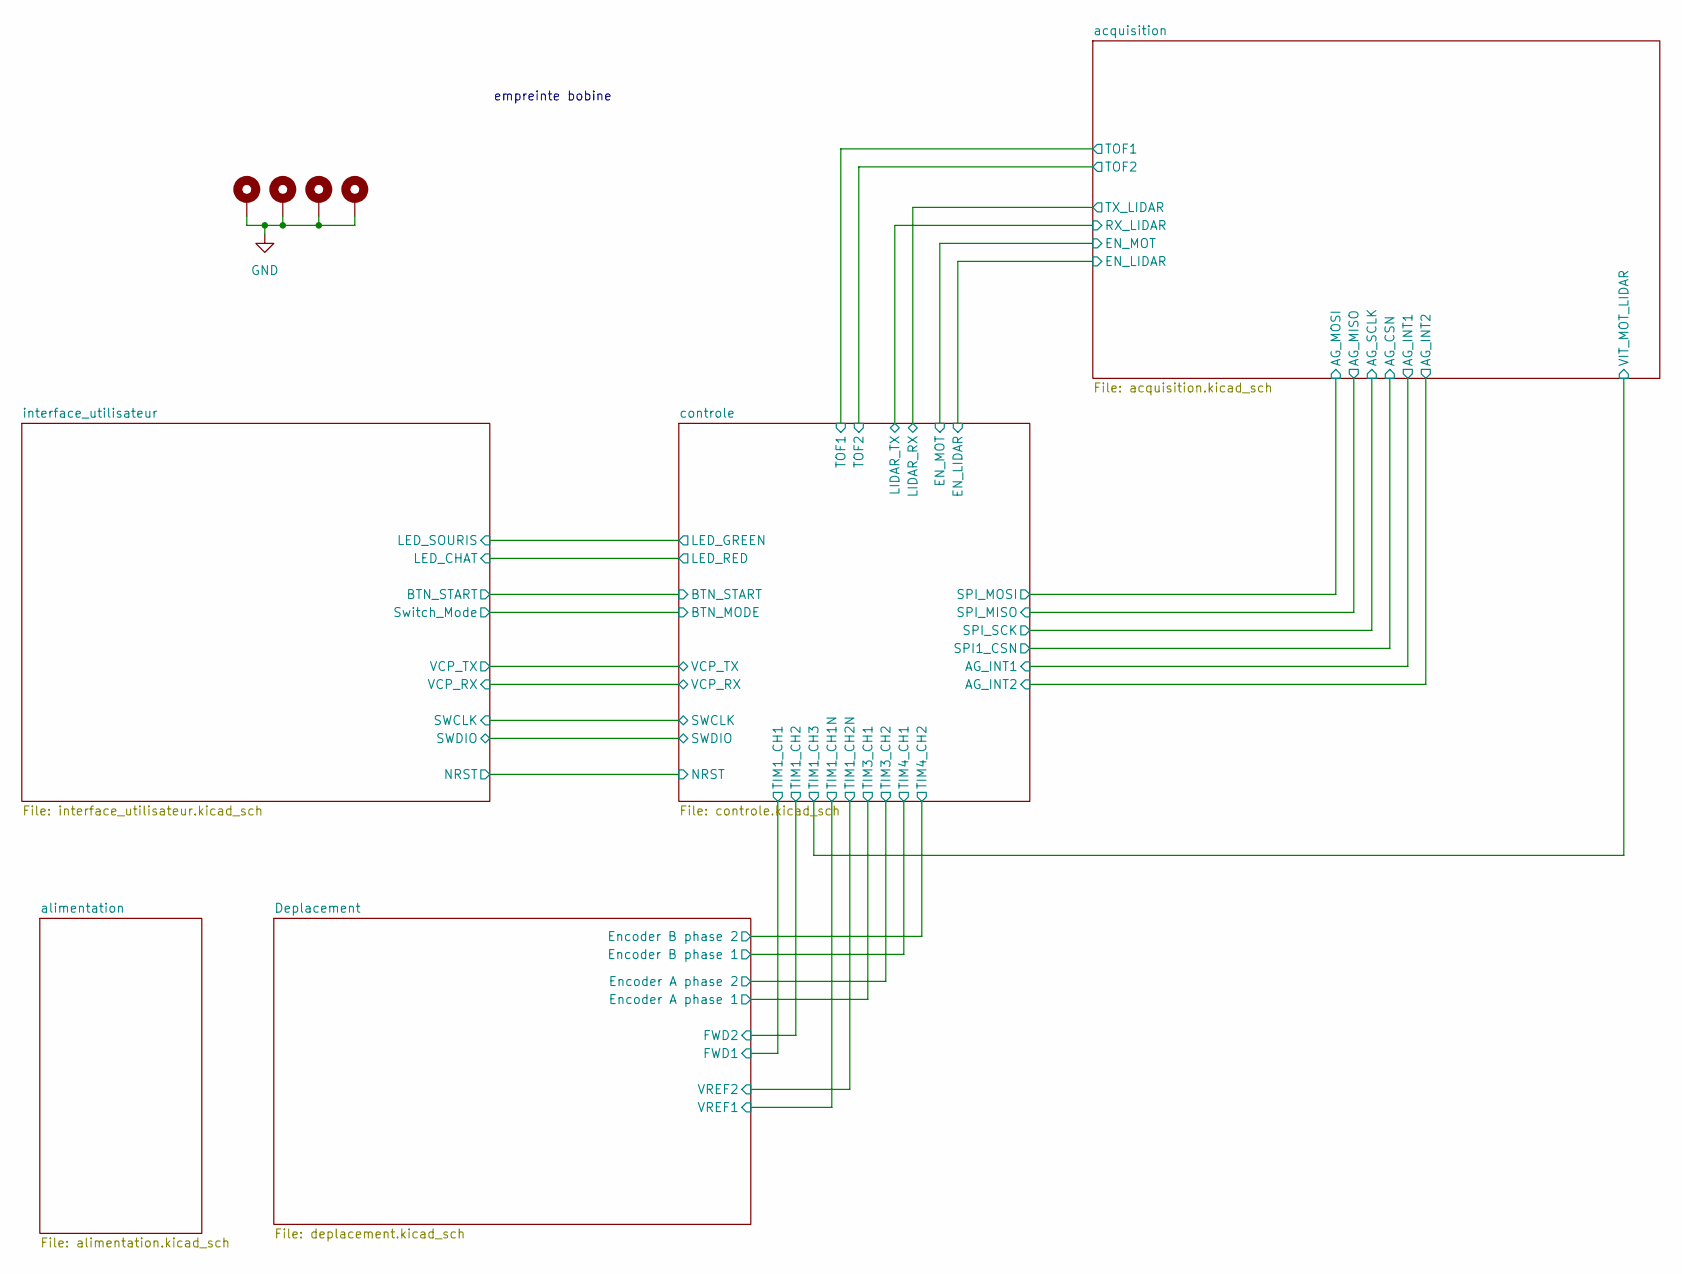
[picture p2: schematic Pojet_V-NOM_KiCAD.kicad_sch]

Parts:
H1, H2, H3, H4: MountingHole_Pad; MountingHole_3.2mm_M3_Pad_Via

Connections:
GND: H1.1, H2.1, H3.1, H4.1; also elsewhere on the board

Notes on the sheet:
empreinte bobine

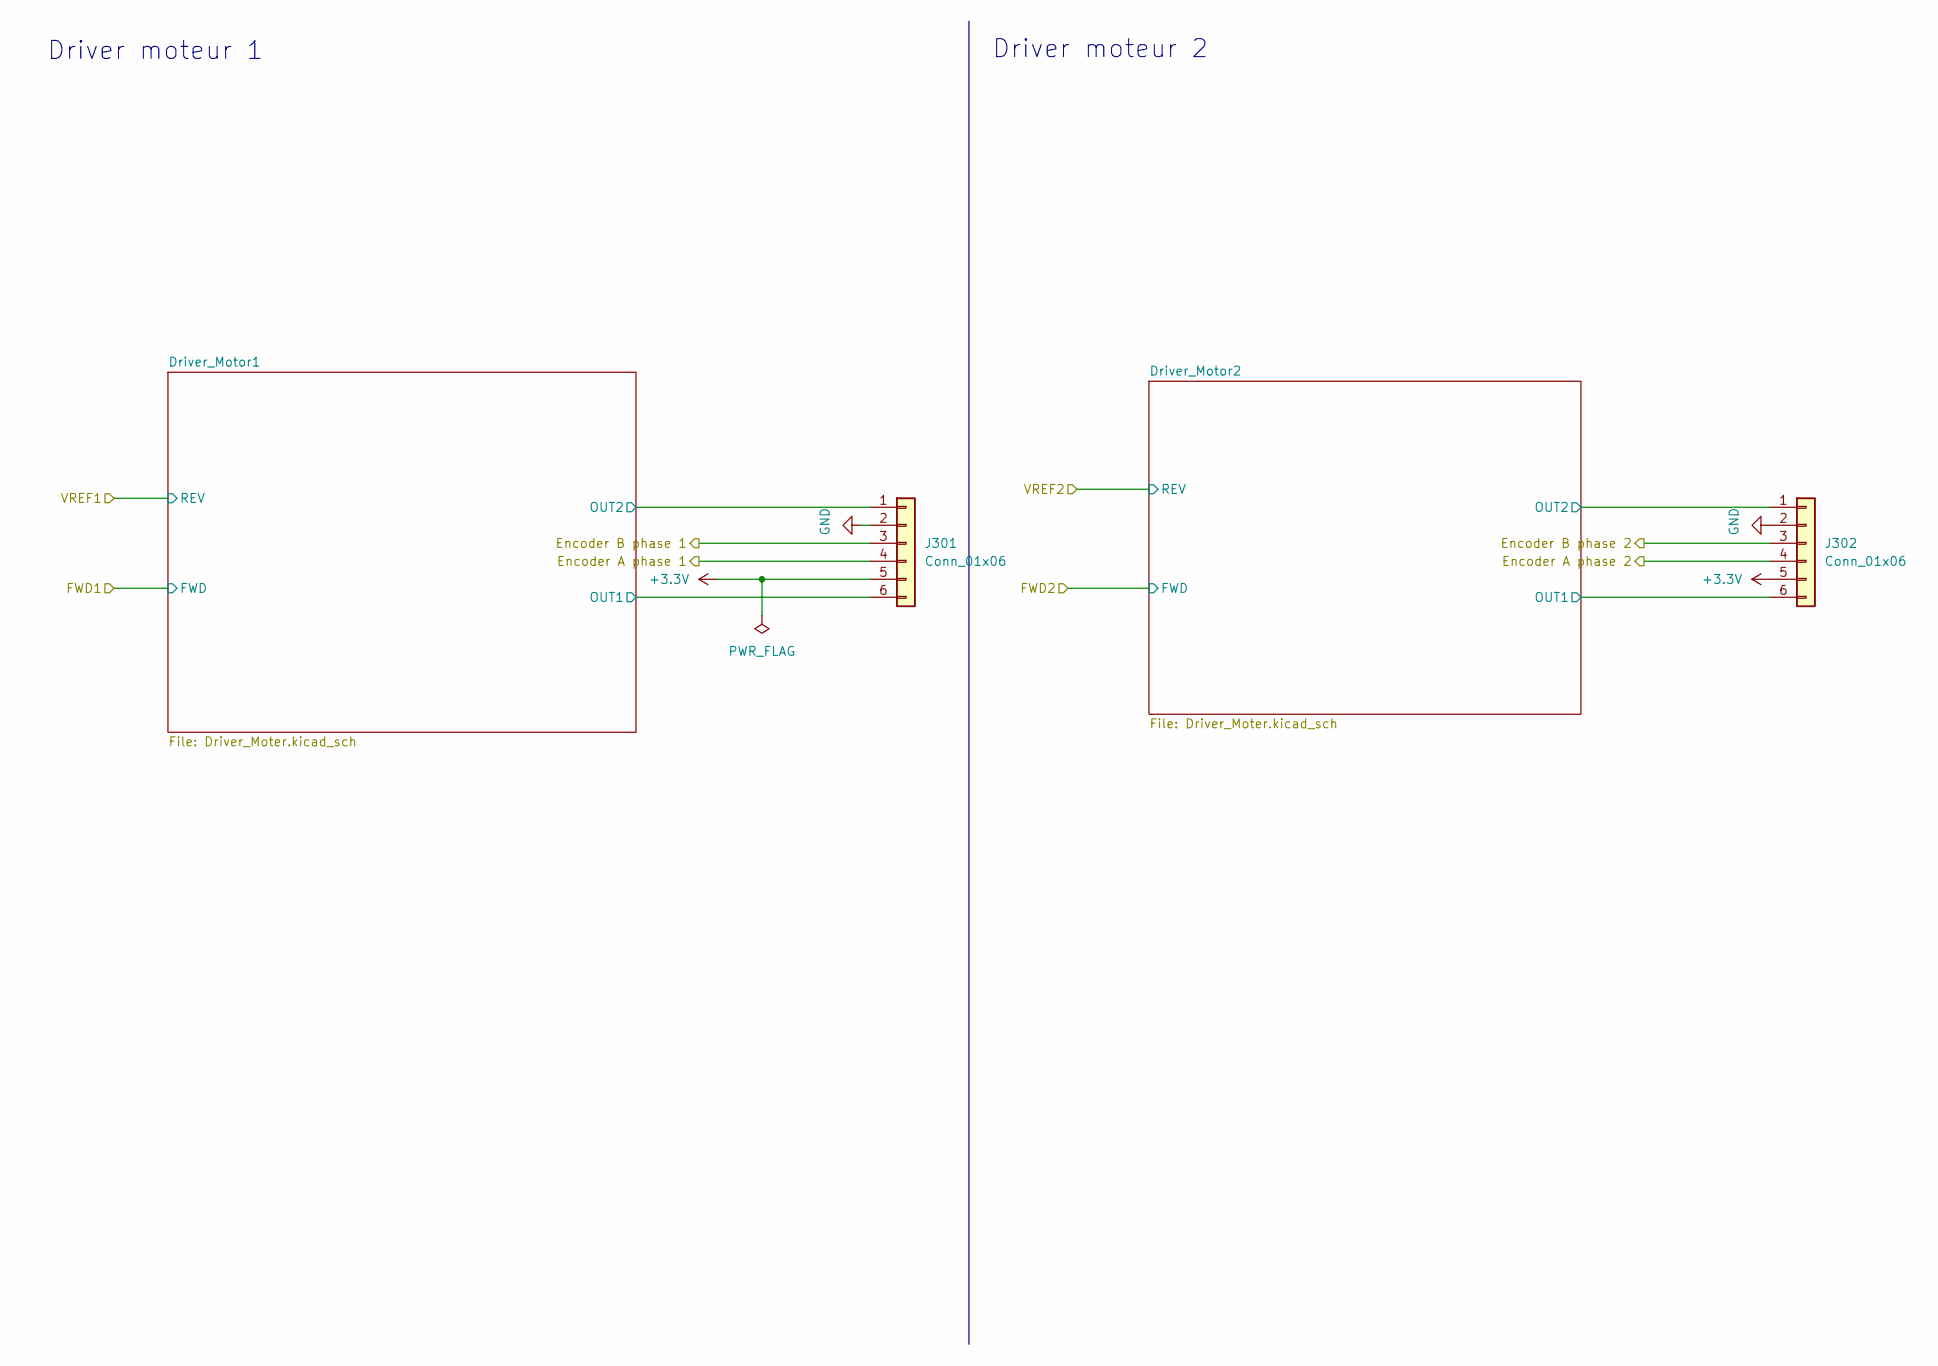
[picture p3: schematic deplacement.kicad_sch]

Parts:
J301, J302: Conn_01x06; JST_XH_S6B-XH-A_1x06_P2.50mm_Horizontal

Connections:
+3.3V: J301.5, J302.5; also elsewhere on the board
/Deplacement/Driver_Motor1/OUT1: J301.6; also elsewhere on the board
/Deplacement/Driver_Motor1/OUT2: J301.1; also elsewhere on the board
/Deplacement/Driver_Motor2/OUT1: J302.6; also elsewhere on the board
/Deplacement/Driver_Motor2/OUT2: J302.1; also elsewhere on the board
/Deplacement/Encoder A phase 1: J301.4; also elsewhere on the board
/Deplacement/Encoder A phase 2: J302.4; also elsewhere on the board
/Deplacement/Encoder B phase 1: J301.3; also elsewhere on the board
/Deplacement/Encoder B phase 2: J302.3; also elsewhere on the board
GND: J301.2, J302.2; also elsewhere on the board

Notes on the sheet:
Driver moteur 2
Driver moteur 1

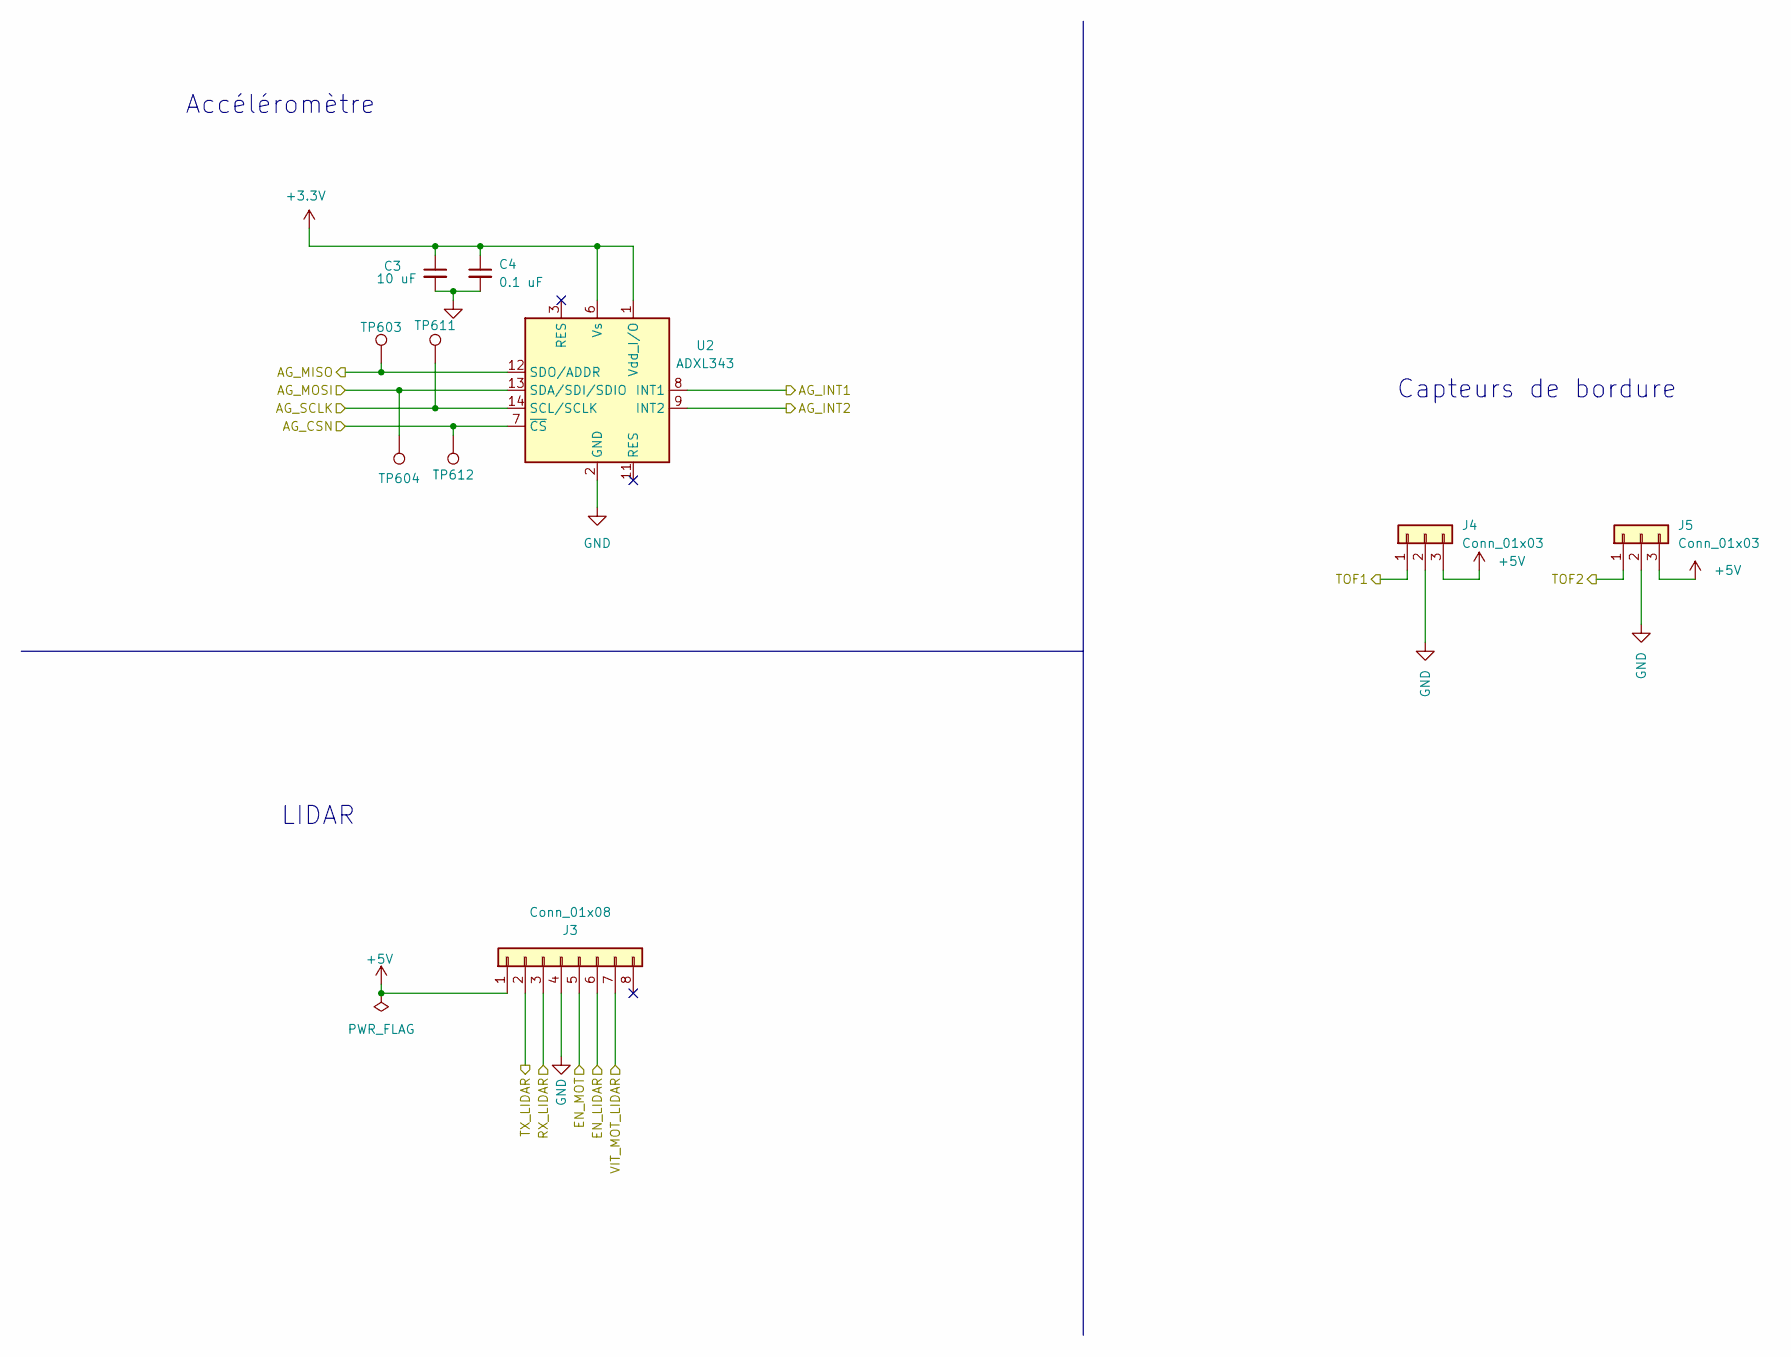
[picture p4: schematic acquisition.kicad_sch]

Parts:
C3: 10 uF; C_0603_1608Metric
C4: 0.1 uF; C_0402_1005Metric
J3: Conn_01x08; JST_XH_S8B-XH-A_1x08_P2.50mm_Horizontal
J4, J5: Conn_01x03; JST_XH_S3B-XH-A_1x03_P2.50mm_Horizontal
TP603, TP604, TP611, TP612: TestPoint; TestPoint_Pad_D1.5mm
U2: ADXL343; LGA-14_3x5mm_P0.8mm_LayoutBorder1x6y

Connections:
+3.3V: C3.1, C4.1, U2.1 (Vdd_I/O), U2.6 (Vs); also elsewhere on the board
+5V: J3.1, J4.3, J5.3; also elsewhere on the board
/acquisition/AG_CSN: TP612.1, U2.7 (~CS); also elsewhere on the board
/acquisition/AG_INT1: U2.8 (INT1); also elsewhere on the board
/acquisition/AG_INT2: U2.9 (INT2); also elsewhere on the board
/acquisition/AG_MISO: TP603.1, U2.12 (SDO/ADDR); also elsewhere on the board
/acquisition/AG_MOSI: TP604.1, U2.13 (SDA/SDI/SDIO); also elsewhere on the board
/acquisition/AG_SCLK: TP611.1, U2.14 (SCL/SCLK); also elsewhere on the board
/acquisition/EN_LIDAR: J3.6; also elsewhere on the board
/acquisition/EN_MOT: J3.5; also elsewhere on the board
/acquisition/RX_LIDAR: J3.3; also elsewhere on the board
/acquisition/TOF1: J4.1; also elsewhere on the board
/acquisition/TOF2: J5.1; also elsewhere on the board
/acquisition/TX_LIDAR: J3.2; also elsewhere on the board
/acquisition/VIT_MOT_LIDAR: J3.7; also elsewhere on the board
GND: C3.2, C4.2, J3.4, J4.2, J5.2, U2.2 (GND), U2.4 (GND), U2.5 (GND); also elsewhere on the board

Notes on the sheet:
LIDAR
Capteurs de bordure
Accéléromètre

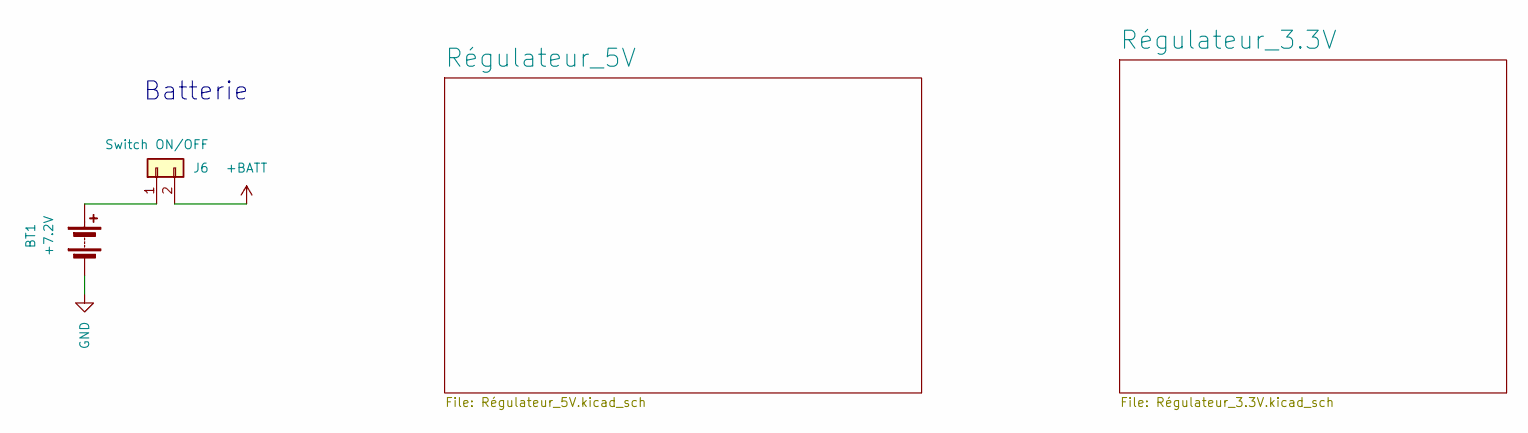
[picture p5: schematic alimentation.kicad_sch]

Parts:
BT1: +7.2V; JST_XH_S2B-XH-A_1x02_P2.50mm_Horizontal
J6: Switch ON/OFF; JST_XH_S2B-XH-A_1x02_P2.50mm_Horizontal

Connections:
+BATT: J6.2; also elsewhere on the board
GND: BT1.2 (-); also elsewhere on the board
unnamed: BT1.1 (+), J6.1

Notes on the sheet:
Batterie

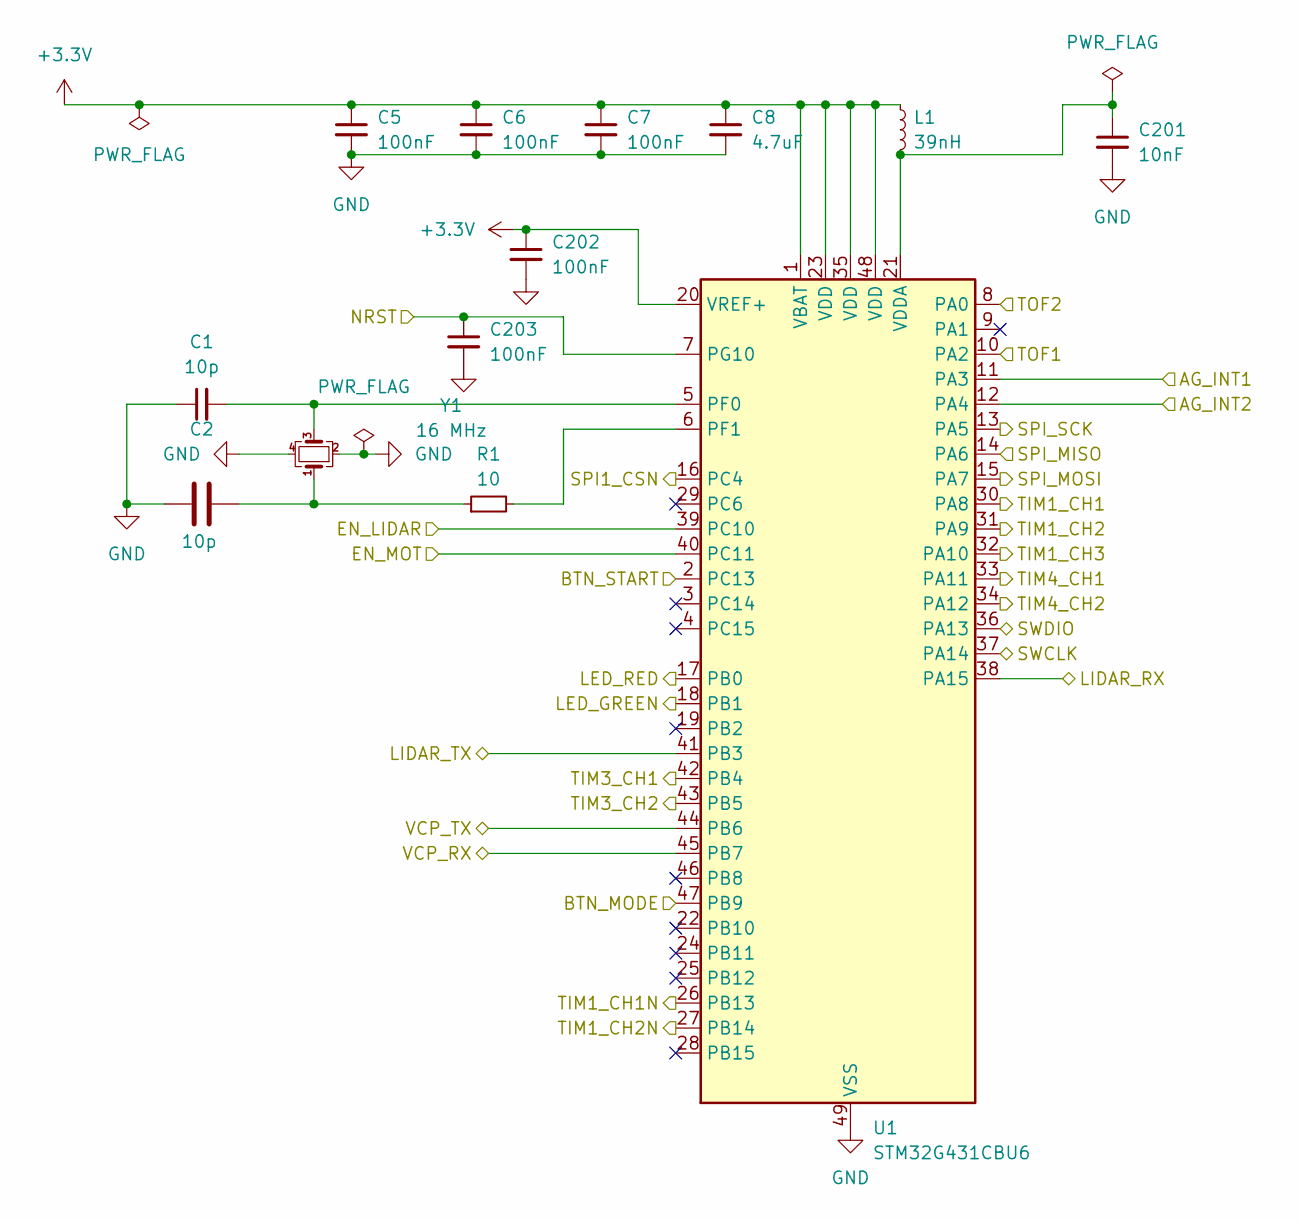
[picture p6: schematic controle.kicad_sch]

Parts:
C1, C2: 10p; C_0402_1005Metric
C5, C6, C7, C202, C203: 100nF; C_0402_1005Metric
C8: 4.7uF; C_0603_1608Metric
C201: 10nF; C_0402_1005Metric
L1: 39nH; L_0402_1005Metric
R1: 10; R_0402_1005Metric
U1: STM32G431CBU6; QFN-48-1EP_7x7mm_P0.5mm_EP5.6x5.6mm
Y1: 16 MHz; Crystal_SMD_EuroQuartz_MT-4Pin_3.2x2.5mm

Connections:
+3.3V: C5.1, C6.1, C7.1, C8.1, C202.1, L1.1, U1.1 (VBAT), U1.20 (VREF+), U1.23 (VDD), U1.35 (VDD), U1.48 (VDD); also elsewhere on the board
/Deplacement/Encoder A phase 1: U1.42 (PB4); also elsewhere on the board
/Deplacement/Encoder A phase 2: U1.43 (PB5); also elsewhere on the board
/Deplacement/Encoder B phase 1: U1.33 (PA11); also elsewhere on the board
/Deplacement/Encoder B phase 2: U1.34 (PA12); also elsewhere on the board
/Deplacement/FWD1: U1.30 (PA8); also elsewhere on the board
/Deplacement/FWD2: U1.31 (PA9); also elsewhere on the board
/Deplacement/VREF1: U1.26 (PB13); also elsewhere on the board
/Deplacement/VREF2: U1.27 (PB14); also elsewhere on the board
/acquisition/AG_CSN: U1.16 (PC4); also elsewhere on the board
/acquisition/AG_INT1: U1.11 (PA3); also elsewhere on the board
/acquisition/AG_INT2: U1.12 (PA4); also elsewhere on the board
/acquisition/AG_MISO: U1.14 (PA6); also elsewhere on the board
/acquisition/AG_MOSI: U1.15 (PA7); also elsewhere on the board
/acquisition/AG_SCLK: U1.13 (PA5); also elsewhere on the board
/acquisition/EN_LIDAR: U1.39 (PC10); also elsewhere on the board
/acquisition/EN_MOT: U1.40 (PC11); also elsewhere on the board
/acquisition/RX_LIDAR: U1.41 (PB3); also elsewhere on the board
/acquisition/TOF1: U1.10 (PA2); also elsewhere on the board
/acquisition/TOF2: U1.8 (PA0); also elsewhere on the board
/acquisition/TX_LIDAR: U1.38 (PA15); also elsewhere on the board
/acquisition/VIT_MOT_LIDAR: U1.32 (PA10); also elsewhere on the board
/controle/BTN_MODE: U1.47 (PB9); also elsewhere on the board
/controle/BTN_START: U1.2 (PC13); also elsewhere on the board
/controle/LED_GREEN: U1.18 (PB1); also elsewhere on the board
/controle/LED_RED: U1.17 (PB0); also elsewhere on the board
/controle/NRST: C203.1, U1.7 (PG10); also elsewhere on the board
/controle/SWCLK: U1.37 (PA14); also elsewhere on the board
/controle/SWDIO: U1.36 (PA13); also elsewhere on the board
/controle/VCP_RX: U1.45 (PB7); also elsewhere on the board
/controle/VCP_TX: U1.44 (PB6); also elsewhere on the board
GND: C1.1, C2.1, C5.2, C6.2, C7.2, C8.2, C201.2, C202.2, C203.2, U1.49 (VSS), Y1.2, Y1.4; also elsewhere on the board
unnamed: C2.2, R1.1, Y1.1
unnamed: C1.2, U1.5 (PF0), Y1.3
unnamed: R1.2, U1.6 (PF1)
unnamed: C201.1, L1.2, U1.21 (VDDA)

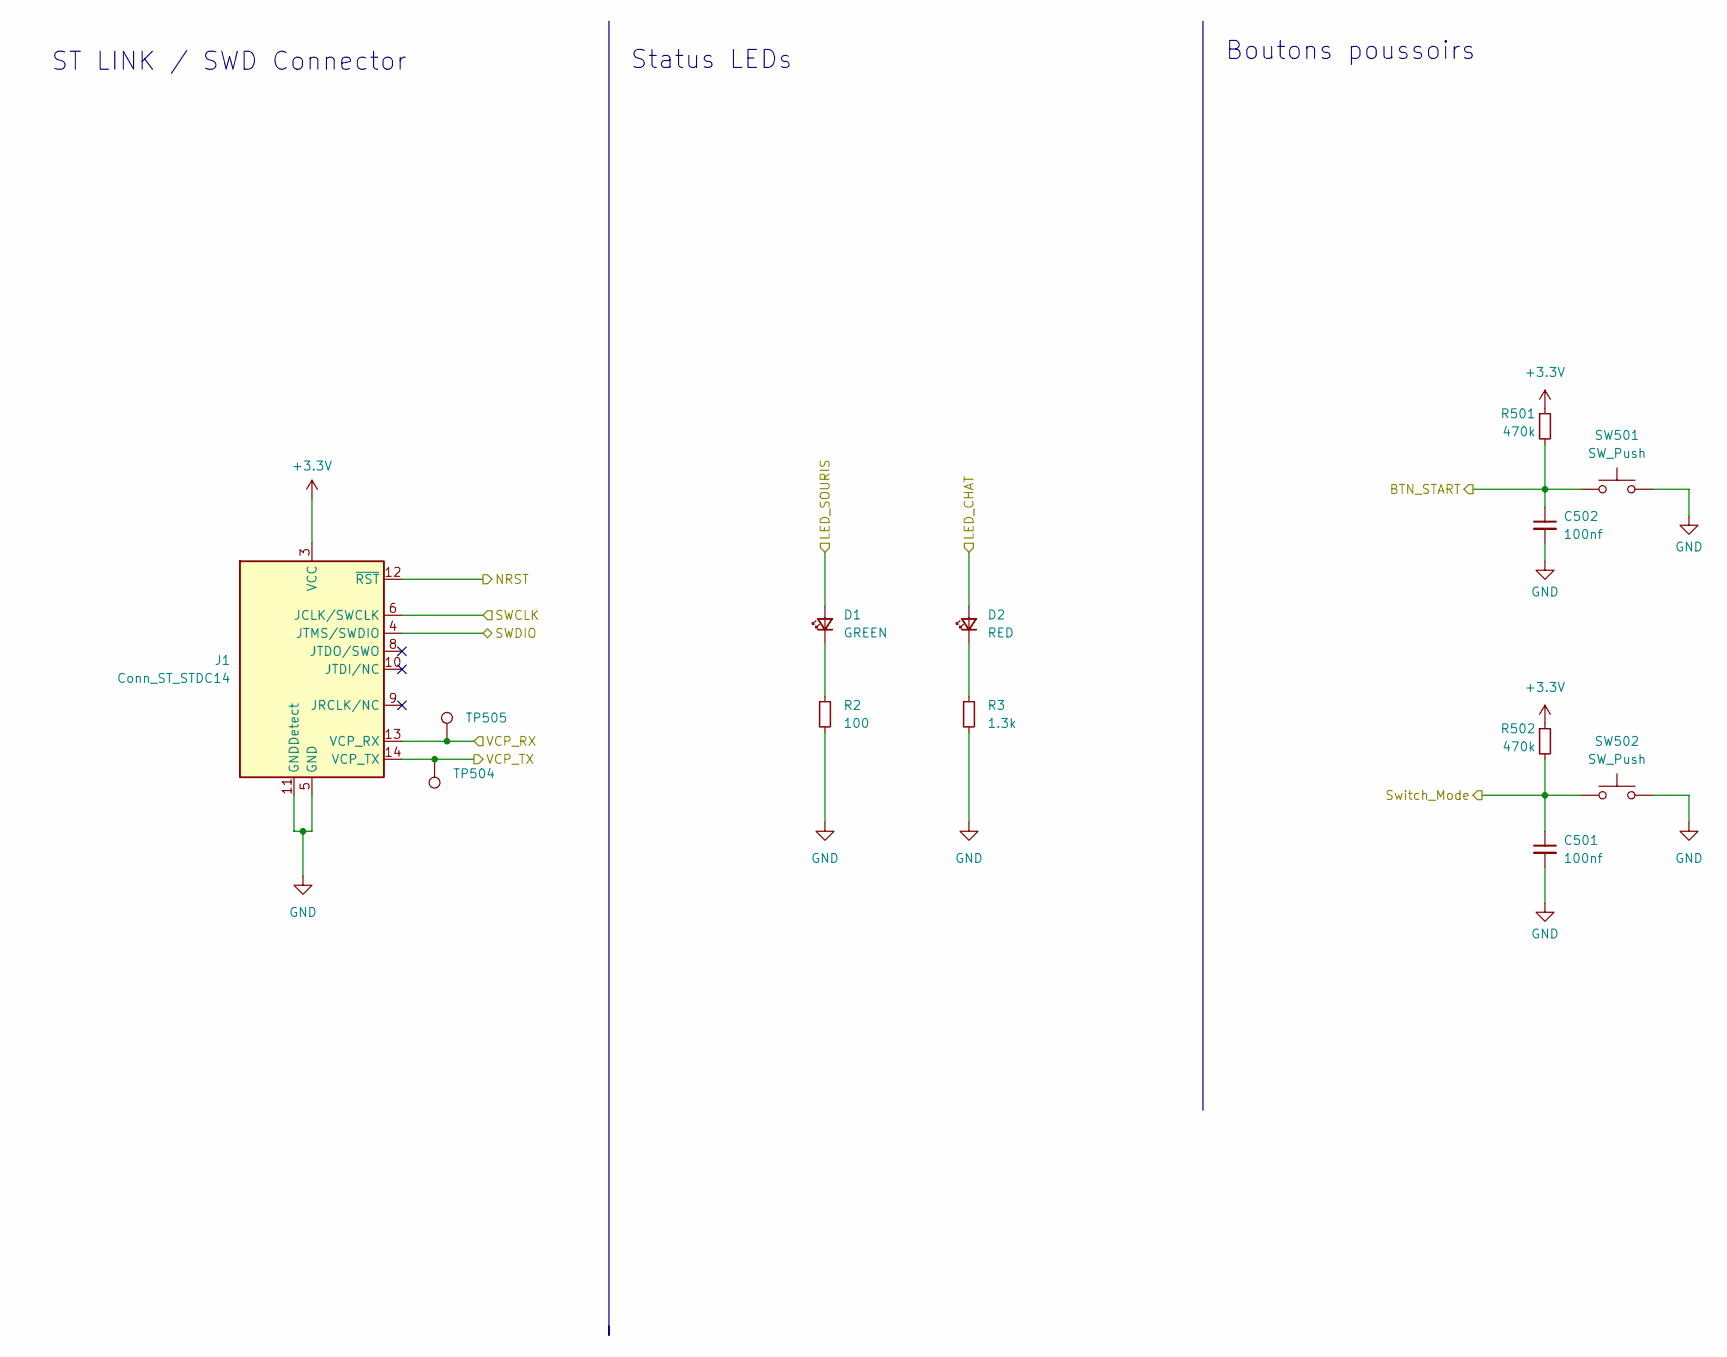
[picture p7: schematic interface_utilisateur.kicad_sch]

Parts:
C501, C502: 100nf; C_0402_1005Metric
D1: GREEN; LED_0603_1608Metric_Pad1.05x0.95mm_HandSolder
D2: RED; LED_0603_1608Metric_Pad1.05x0.95mm_HandSolder
J1: Conn_ST_STDC14; PinHeader_2x07_P1.27mm_Vertical_SMD
R2: 100; R_0402_1005Metric
R3: 1.3k; R_0402_1005Metric
R501, R502: 470k; R_0402_1005Metric
SW501, SW502: SW_Push; SW_Push_1P1T_NO_6x6mm_H9.5mm
TP504, TP505: TestPoint; TestPoint_Pad_D1.5mm

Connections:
+3.3V: J1.3 (VCC), R501.1, R502.1; also elsewhere on the board
/controle/BTN_MODE: C501.1, R502.2, SW502.1; also elsewhere on the board
/controle/BTN_START: C502.1, R501.2, SW501.1; also elsewhere on the board
/controle/LED_GREEN: D1.2 (A); also elsewhere on the board
/controle/LED_RED: D2.2 (A); also elsewhere on the board
/controle/NRST: J1.12 (~RST); also elsewhere on the board
/controle/SWCLK: J1.6 (JCLK/SWCLK); also elsewhere on the board
/controle/SWDIO: J1.4 (JTMS/SWDIO); also elsewhere on the board
/controle/VCP_RX: J1.13 (VCP_RX), TP505.1; also elsewhere on the board
/controle/VCP_TX: J1.14 (VCP_TX), TP504.1; also elsewhere on the board
GND: C501.2, C502.2, J1.5 (GND), J1.7 (GND), J1.11 (GNDDetect), R2.2, R3.2, SW501.2, SW502.2; also elsewhere on the board
unnamed: D1.1 (K), R2.1
unnamed: D2.1 (K), R3.1

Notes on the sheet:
ST LINK / SWD Connector
Status LEDs
Boutons poussoirs

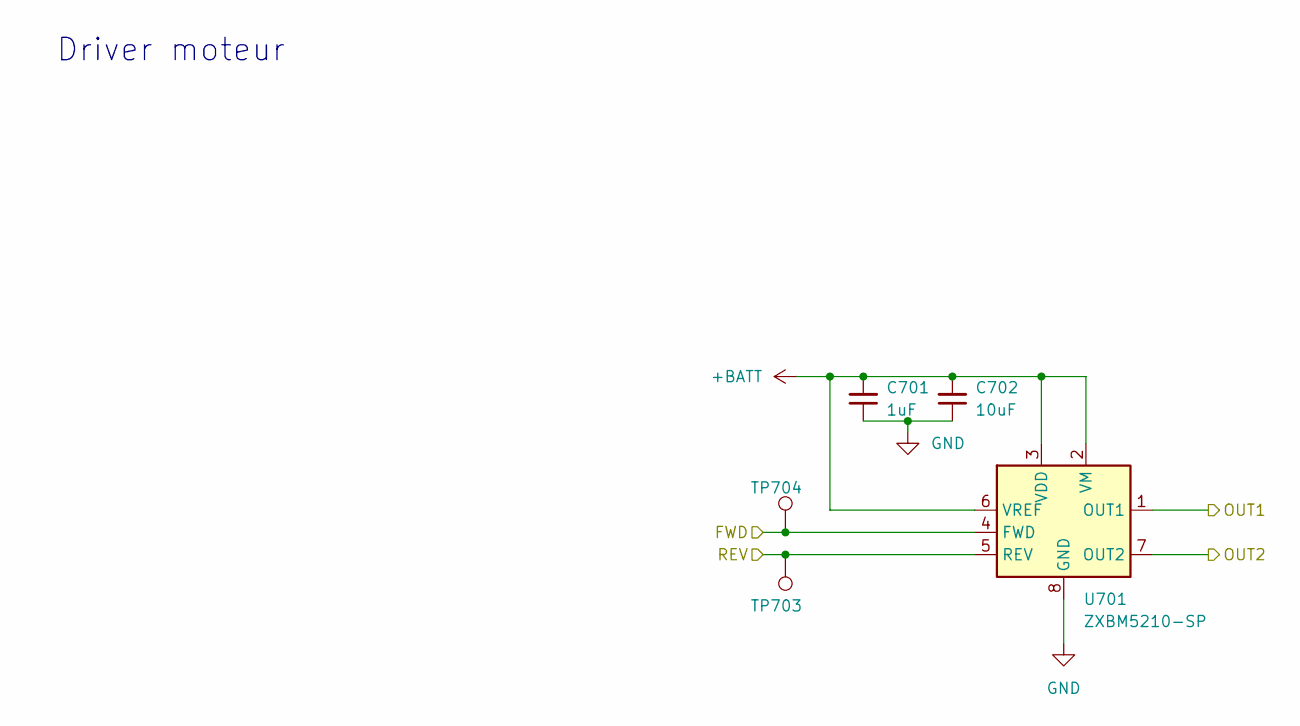
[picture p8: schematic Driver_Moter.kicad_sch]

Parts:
C701: 1uF; C_0603_1608Metric
C702: 10uF; C_0603_1608Metric
TP703, TP704: TestPoint; TestPoint_Pad_D1.5mm
U701: ZXBM5210-SP; Diodes_SO-8EP

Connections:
+BATT: C701.2, C702.2, U701.2 (VM), U701.3 (VDD), U701.6 (VREF); also elsewhere on the board
/Deplacement/Driver_Motor1/OUT1: U701.1 (OUT1); also elsewhere on the board
/Deplacement/Driver_Motor1/OUT2: U701.7 (OUT2); also elsewhere on the board
/Deplacement/FWD1: TP704.1, U701.4 (FWD); also elsewhere on the board
/Deplacement/VREF1: TP703.1, U701.5 (REV); also elsewhere on the board
GND: C701.1, C702.1, U701.8 (GND), U701.9 (GND); also elsewhere on the board

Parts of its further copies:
C801: 1uF; C_0603_1608Metric
C802: 10uF; C_0603_1608Metric
TP803, TP804: TestPoint; TestPoint_Pad_D1.5mm
U801: ZXBM5210-SP; Diodes_SO-8EP

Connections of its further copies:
+BATT: C801.2, C802.2, U801.2 (VM), U801.3 (VDD), U801.6 (VREF); also elsewhere on the board
/Deplacement/Driver_Motor2/OUT1: U801.1 (OUT1); also elsewhere on the board
/Deplacement/Driver_Motor2/OUT2: U801.7 (OUT2); also elsewhere on the board
/Deplacement/FWD2: TP804.1, U801.4 (FWD); also elsewhere on the board
/Deplacement/VREF2: TP803.1, U801.5 (REV); also elsewhere on the board
GND: C801.1, C802.1, U801.8 (GND), U801.9 (GND); also elsewhere on the board

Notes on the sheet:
Driver moteur

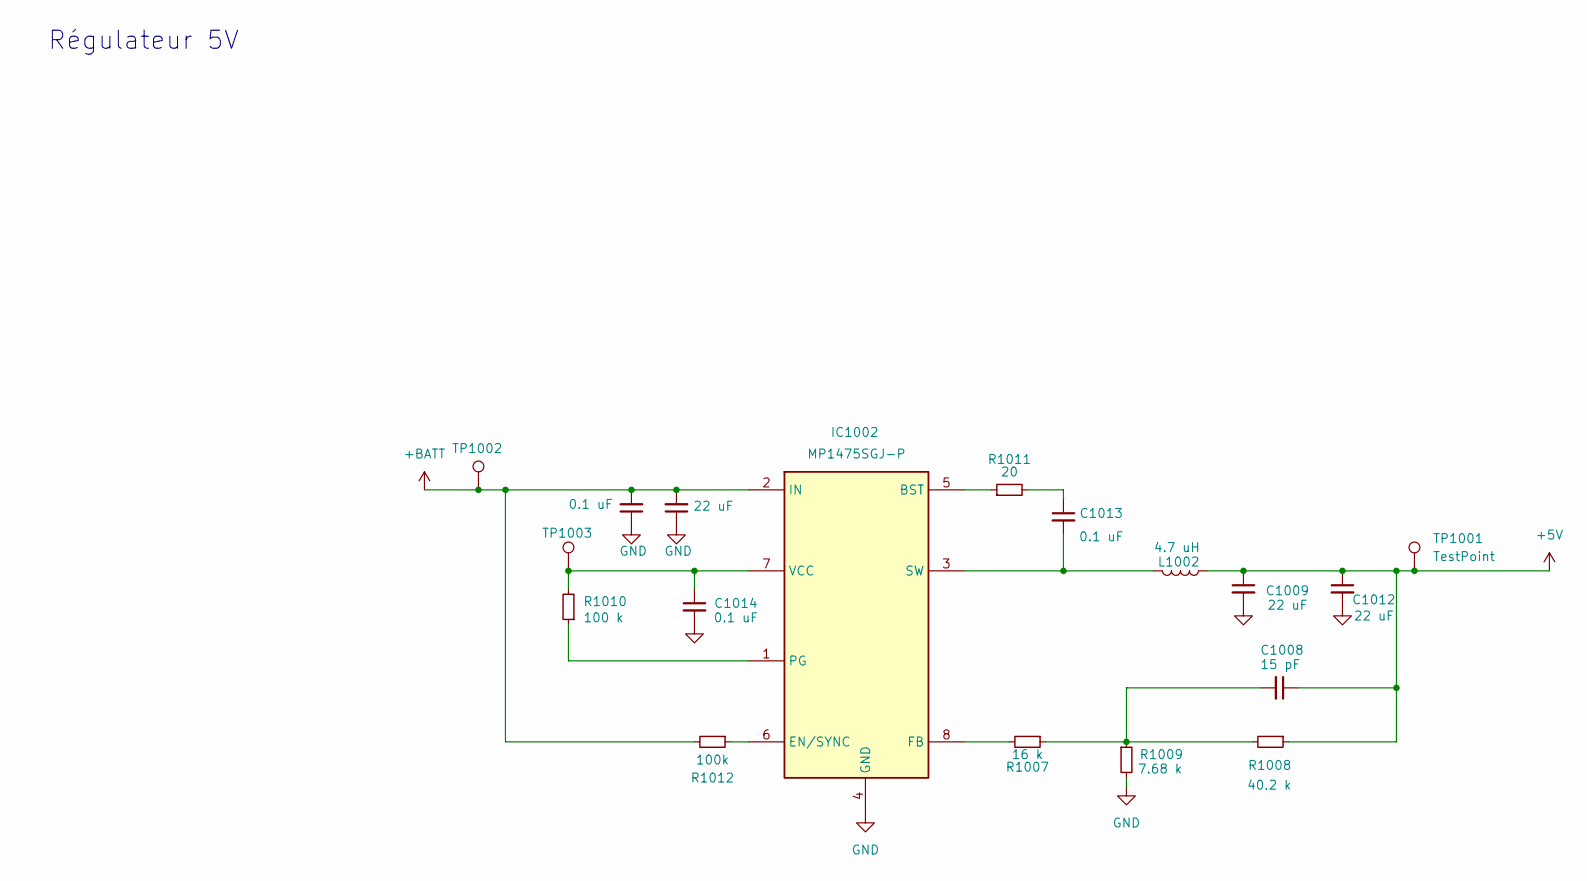
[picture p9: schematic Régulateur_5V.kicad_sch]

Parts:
C1008: 15 pF; C_0402_1005Metric
C1009, C1010, C1012: 22 uF; C_0805_2012Metric
C1011, C1013, C1014: 0.1 uF; C_0402_1005Metric
IC1002: MP1475SGJ-P; SOT-23-8; Manufacturer_Part_Number MP1475SGJ-P; Mouser Part Number 946-MP1475SGJ-P
L1002: 4.7 uH; Inductance L1
R1007: 16 k; R_0402_1005Metric
R1008: 40.2 k; R_0402_1005Metric
R1009: 7.68 k; R_0402_1005Metric
R1010: 100 k; R_0402_1005Metric
R1011: 20; R_0402_1005Metric
R1012: 100k; R_0402_1005Metric
TP1001, TP1002, TP1003: TestPoint; TestPoint_Pad_D1.5mm

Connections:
+5V: C1008.1, C1009.1, C1012.1, L1002.1, R1008.1, TP1001.1; also elsewhere on the board
+BATT: C1010.2, C1011.2, IC1002.2 (IN), R1012.2, TP1002.1; also elsewhere on the board
GND: C1009.2, C1010.1, C1011.1, C1012.2, C1014.2, IC1002.4 (GND), R1009.2; also elsewhere on the board
unnamed: C1008.2, R1007.1, R1008.2, R1009.1
unnamed: C1013.1, R1011.2
unnamed: IC1002.5 (BST), R1011.1
unnamed: IC1002.6 (EN/SYNC), R1012.1
unnamed: IC1002.8 (FB), R1007.2
unnamed: IC1002.1 (PG), R1010.1
unnamed: C1013.2, IC1002.3 (SW), L1002.2
unnamed: C1014.1, IC1002.7 (VCC), R1010.2, TP1003.1

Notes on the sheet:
Régulateur 5V

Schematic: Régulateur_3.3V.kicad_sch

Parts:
C901, C902: 1uF; C_0603_1608Metric
PS901: BU33SD5WG-TR; SOT-23-5; Manufacturer_Part_Number BU33SD5WG-TR; Mouser Part Number 755-BU33SD5WG-TR
TP901: TestPoint; TestPoint_Pad_D1.5mm

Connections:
+3.3V: C902.1, PS901.5 (VOUT), TP901.1; also elsewhere on the board
+5V: C901.1, PS901.1 (VIN), PS901.3 (STBY); also elsewhere on the board
GND: C901.2, C902.2, PS901.2 (GND); also elsewhere on the board

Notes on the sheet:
Régulateur 3.3V

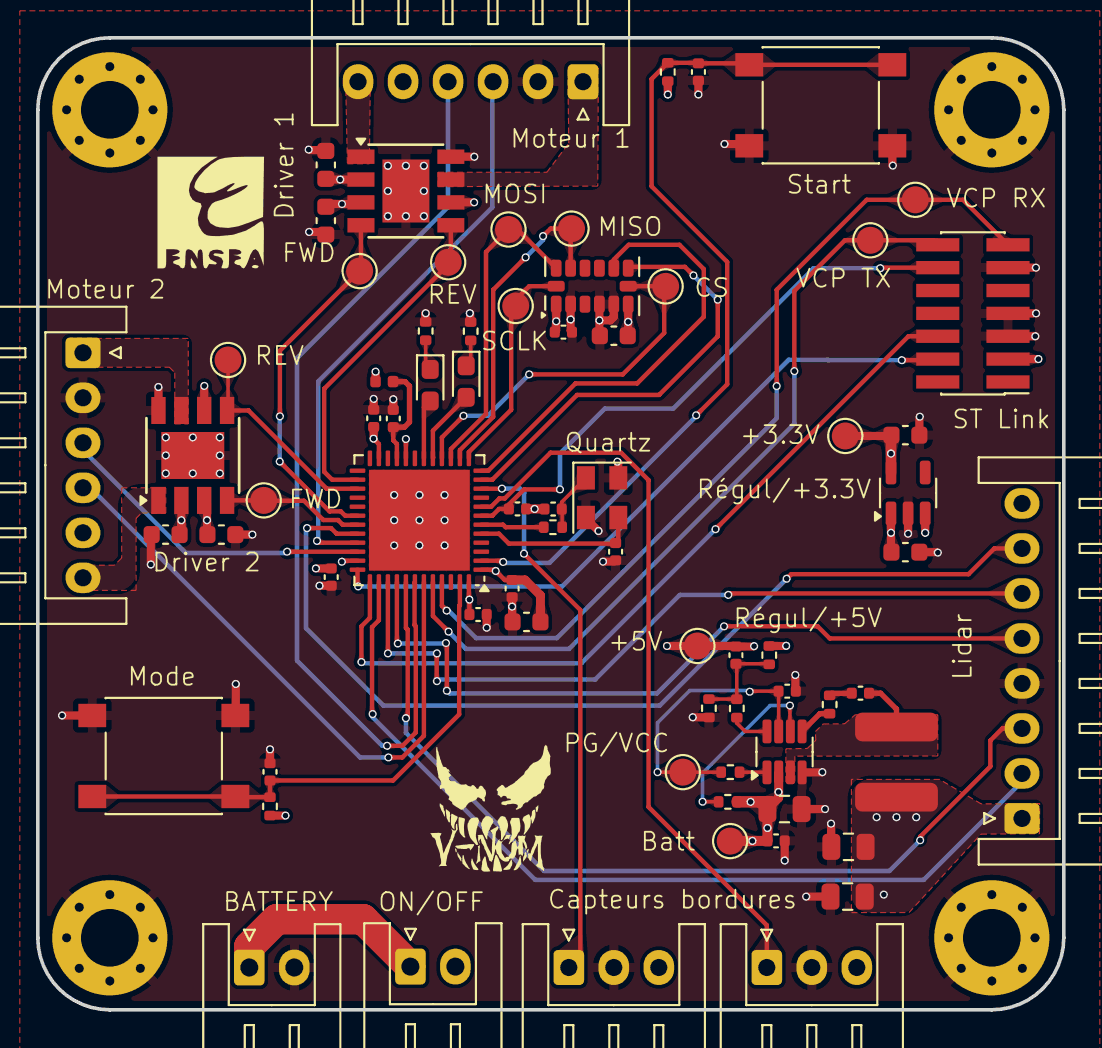
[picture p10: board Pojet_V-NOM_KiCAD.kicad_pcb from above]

Board: 4 copper layers, 57.0 x 54.0 mm, 76 parts (0 on the bottom side), 53 nets.

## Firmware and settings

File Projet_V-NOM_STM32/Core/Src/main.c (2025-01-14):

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
/* Includes ------------------------------------------------------------------*/
#include "main.h"
#include "cmsis_os.h"
#include "adc.h"
#include "dma.h"
#include "spi.h"
#include "tim.h"
#include "usart.h"
#include "gpio.h"

/* USER CODE BEGIN Includes */
#include <stdio.h>
#include <stdlib.h>
#include "stm32g4xx_hal.h"

// Drivers
#include "../drivers/driver_Motor.h"
#include "../drivers/driver_GP2Y0A41SK0F.h"
#include "../drivers/driver_YLIDARX2.h"
#include "../drivers/driver_ADXL343.h"

/* USER CODE END Includes */

/* USER CODE BEGIN PD */
#define DEBUG 1 /**< Enable or disable debug logs */

#if DEBUG
#define DEBUG_PRINT(...) printf(__VA_ARGS__)
#else
#define DEBUG_PRINT(...)
#endif

#define STACK_SIZE 256
#define TASK_PRIORITY_MOTOR 10
#define TASK_PRIORITY_CONTROL 2

#define TOF_TRESHHOLD 40 /**< Threshhold for edge detection */

#define DEBOUNCE_DELAY_MS 50 /**< Debounce delay in milliseconds */

/* USER CODE END PD */


/* USER CODE BEGIN PV */
// Messages
char small_logo_msg[] ="\r\n"
		"       \\_______/\r\n"
		"   `.,-'\\_____/`-.,'\r\n"
		"    /`..'\\ _ /`.,'\\\r\n"
		"   /  /`.,' `.,'\\  \\\r\n"
		"__/__/__/V-NOM\\__\\__\\__\r\n"
		"  \\  \\  \\     /  /  /\r\n"
		"   \\  \\,'`._,'`./  /\r\n"
		"    \\,'`./___\\,'`./\r\n"
		"   ,'`-./_____\\,-'`.\r\n"
		"       /       \\ \r\n";

char big_logo_msg[] = "\r\n"
		"⠀⠀⠀⠀⠀⠀⠀⠀⢀⣀⣤⠤⠶⠶⠶⠤⠤⣤⣀\t\r\n"
		"⠀⠀⠀⠀⢀⣠⠶⠛⠉⠀⠀⠀⠀⠀⠀⠀⠀⠀⠈⠙⠳⢦⣀\t\r\n"
		"⠀⠀⠀⣰⠟⠁⠀⠀⠀⠀⠀⠀⠀⠀⠀⠀⠀⠀⠀⠀⠀⠀⠙⢷⡄\t\r\n"
		"⠀⠀⣰⠏⠀⢠⣶⠀⠀⠀⠀⠀⠀⠀⠀⠀⠀⠀⠀⠀⠀⣤⡀⠀⠹⣆\t\r\n"
		"⠀⢠⡏⠀⢠⠟⣧⠀⠀⠀⠀⠀⠀⠀⠀⠀⠀⠀⠀⠀⠀⣿⢳⡄⠀⢹⡄\t\r\n"
		"⠀⣾⠀⠀⡞⠀⢸⡀⠀⠀⠀⠀⠀⠀⠀⠀⠀⠀⠀⠀⣰⠇⠀⢷⠀⠈⣇\t\r\n"
		"⢠⡇⠀⢠⠇⠀⠀⠙⣆⠀⠀⠀⠀⠀⠀⠀⠀⠀⠀⣰⠋⠀⠀⠸⡆⠀⣿\t\r\n"
		"⢸⡇⠀⢸⠀⠀⠀⠀⠙⢦⡀⠀⠀⠀⠀⠀⠀⢀⡾⠃⠀⠀⠀⢰⠇⠀⣿\t\r\n"
		"⢸⡇⠀⢸⠀⠀⠀⠀⠀⠀⠳⣄⣰⡄⢰⣄⣰⠋⠀⠀⠀⠀⠀⢸⡀⠀⣿\t\r\n"
		"⠘⡇⠀⢸⠀⠀⠀⠀⠀⠀⠀⠈⢹⡇⢸⠉⠁⠀⠀⠀⠀⠀⠀⠈⡇⠀⡟\t\r\n"
		"⠀⢿⠀⠈⢧⡀⠀⠀⠀⠀⠀⠀⣾⠀⢸⣄⠀⠀⠀⠀⠀⠀⠀⡼⢁⢸⡇\t\r\n"
		"⠀⢸⠘⣆⠈⢧⠀⠀⠀⠀⣠⠴⠃⠀⠀⠙⢧⣀⠀⠀⠀⠀⡼⠀⡼⢸⡃⠀⠀⠀⠀⠀⢀\t\r\n"
		"⠀⣾⠀⢸⣆⠘⠷⠤⠴⠚⣁⣀⣤⣤⣤⣄⣀⠉⠙⠲⠴⠚⢡⣾⠇⠘⡇⠀⠀⠀⠀⠀⠈⢷⣤⡀\t\r\n"
		"⠀⢹⣆⠈⣿⣷⣾⡖⣾⠻⣟⣾⣏⣻⣹⡟⡟⣿⢳⣶⣶⣾⣿⡟⠀⢰⡇⠀⠀⠀⠀⠀⠀⠘⣇⢻⡄\t\r\n"
		"⠀⠀⠻⣄⢸⣿⡋⠹⠿⣿⣿⡿⢿⣿⡟⣿⢿⣿⡟⠹⠋⠙⡿⠁⣴⠟⠀⠀⠀⠀⠀⠀⠀⠀⣿⠀⣷\t\r\n"
		"⠀⠀⠀⠹⣶⣿⣿⣄⠀⢻⣘⣦⣼⣿⣴⣿⣼⣼⣇⡀⣰⣿⠃⣴⠏⠀⠀⠀⠀⠀⠀⠀⢀⣴⠏⢀⡏\t\r\n"
		"⠀⠀⠀⠀⠙⣿⢿⣿⣥⣾⠛⠉⠀⠀⠉⠙⢦⡀⠈⠙⢿⣇⣰⠃⠀⠀⠀⠀⣀⣀⡤⠶⠛⠁⢠⡾⠁\t\r\n"
		"⠀⠀⠀⠀⠀⠘⣿⠻⣿⢻⣦⠀⢀⡀⠀⠀⠀⠙⠀⠀⠀⠹⣇⠀⠀⢀⣴⠟⠉⠀⠀⢀⣠⡼⠋\t\r\n"
		"⠀⠀⠀⠀⠀⠀⠘⣿⢹⡾⢻⣇⣴⡿⠳⢦⣀⠀⠀⠀⠀⠀⠙⠳⠶⠛⠁⠀⠀⢀⡼⠋⠁\t\r\n"
		"⠀⠀⠀⠀⠀⠀⠀⠘⣿⠻⡎⢹⢿⣷⣶⣎⣿⣧⡀⠀⠀⠀⠀⠀⠀⠀⠀⠀⢀⡾⠁\t\r\n"
		"⠀⠀⠀⠀⠀⠀⠀⠀⠸⣆⠙⢾⣸⠙⡿⢿⣩⠏⢹⣦⣀⠀⠀⠀⠀⠀⢀⣴⠟⠁\t\r\n"
		"⠀⠀⠀⠀⠀⠀⠀⠀⠀⠹⣦⡀⠉⠉⠉⠉⠁⣰⠏⠀⠈⠉⠛⠒⠒⠛⠉⠁\t\r\n"
		"⠀⠀⠀⠀⠀⠀⠀⠀⠀⠀⠈⠉⠓⠒⠒⠒⠋⠁\t\r\n";

char jumbo_logo_msg[] = "\r\n"
		"⣿⣿⣿⣿⣿⣿⣿⠿⢻⣿⣿⣿⣿⣿⣿⣿⣿⣿⣿⣿⣿⣿⣿⣿⣿⣿⣿⣿⣿⣿⣿⡟⠻⣿⣿⣿⣿⣿⣿⣿\r\n"
		"⣿⣿⣿⣿⣿⠟⠁⢠⣿⣿⣿⣿⣿⣿⣿⣿⣿⣿⣿⣿⣿⣿⣿⣿⣿⣿⣿⣿⣿⣿⣿⡇⠀⠀⠙⣿⣿⣿⣿⣿\r\n"
		"⣿⣿⣿⣿⠃⠀⢀⣿⣿⣿⣿⣿⣿⣿⣿⣿⣿⣿⣿⣿⣿⣿⣿⣿⣿⣿⣿⣿⣿⣿⣿⣷⠀⠀⠀⠈⢻⣿⣿⣿\r\n"
		"⣿⣿⣟⠁⠀⠀⢸⣿⣿⣿⣿⣿⣿⣿⣿⣿⣿⣿⣿⣿⣿⣿⣿⣿⣿⣿⣿⣿⣿⣿⣿⠇⢀⡀⠀⠀⠈⢿⣿⣿\r\n"
		"⣿⣿⡏⠀⠀⠀⢸⣿⣿⣿⣿⣿⣿⣿⣿⣿⣿⣿⣿⣿⣿⣿⣿⣿⣿⣿⣿⣿⣿⣿⣿⣟⣼⣿⠀⠀⠀⠈⣿⣿\r\n"
		"⣿⣿⠀⠀⠀⠀⠸⣿⣿⣿⣿⣿⣿⣿⣿⣿⣿⣿⣿⣿⣿⣿⣿⣿⣿⣿⣿⣿⣿⣿⣿⣿⣿⡏⠀⠀⠀⠀⢹⣿\r\n"
		"⣿⡿⠀⠀⠀⠀⠀⢿⣿⣿⣿⣿⣿⣿⣿⣿⣿⣿⢿⣿⣿⣿⣿⣿⣿⣿⣿⣿⣿⣿⣿⣿⣿⠁⠀⠀⠀⠀⠈⣿\r\n"
		"⣿⡇⠀⠀⠀⠀⠀⠈⠉⠉⣻⣿⡿⣿⣿⣿⣿⢷⣺⣿⣿⣿⣿⣿⣿⣿⣿⣭⣭⣙⣿⠋⠁⠀⠀⠀⠀⠀⠀⣿\r\n"
		"⣿⡷⡶⠀⠀⠀⠀⠀⠀⠈⠋⠛⠻⠿⠿⣿⡟⢿⣿⣿⣿⣿⡿⠿⡿⡿⣿⣻⣿⡿⠁⠀⠀⠀⠀⠀⠀⠀⢸⣿\r\n"
		"⣿⣿⠀⠀⠀⠀⠀⠀⠀⠀⠀⠀⠰⠦⠐⠛⢻⣿⣿⣿⣿⣿⣇⣼⣿⣿⣿⣿⠋⠀⠀⠀⠀⠀⠀⠀⠀⠀⢸⣿\r\n"
		"⣿⣿⡄⠀⠀⠀⠀⠀⠀⠀⠀⠀⠀⠘⣿⣯⣽⣿⣿⣿⣿⣿⣿⣿⣿⣿⣿⠃⠀⠀⠀⠀⠀⠀⠀⠀⠀⠀⢸⣿\r\n"
		"⣿⣿⣇⠀⠀⠀⠀⠀⠀⠀⠀⠀⠀⠀⢸⡟⢿⣿⣿⣿⣿⣿⣿⣿⢃⣿⠇⠀⠀⠀⠀⠀⠀⠀⠀⠀⠀⢀⣿⣿\r\n"
		"⣿⣿⣿⡇⢀⣀⠀⠀⠀⠀⠀⠀⠀⠀⠈⠻⣮⣿⣿⣿⣿⣿⣿⡟⠿⠋⠀⠀⠀⠀⠀⠀⠀⠀⡀⠀⠀⣾⣿⣿\r\n"
		"⣿⣿⣿⡗⠈⣿⣿⣆⠀⠀⠀⠀⠀⠀⠀⠀⢀⡸⣿⣿⣿⣿⡏⠀⠀⠀⠀⠀⠀⠀⠀⠀⣰⣾⣧⡄⢀⣿⣿⣿\r\n"
		"⣿⣿⣿⣿⣤⣿⣿⣿⣷⣄⣀⣴⣶⣶⣶⣤⣄⣹⣿⣿⣿⣿⠀⠀⢀⣀⠶⣄⣀⣤⡶⠾⢿⣿⣿⣷⣿⣿⣿⣿\r\n"
		"⣿⣿⣿⣿⣿⣿⣿⣿⣿⡿⣿⣿⣿⣿⣿⣿⣿⣿⣿⣿⣿⣿⢺⣷⢿⣿⣾⣿⣿⣿⣿⣿⣿⣿⣿⣿⣿⣿⣿⣿\r\n"
		"⣿⣿⣿⣯⣿⠛⠃⣿⢹⢷⣿⣿⣿⣿⣿⣿⣿⣿⣿⣿⣿⣿⣾⣿⣾⣿⣿⣿⡿⣿⢿⠛⣿⣿⣿⣿⣿⣿⣿⣿\r\n"
		"⣿⣿⣿⣿⣿⣿⣧⡇⡈⢹⣿⠉⢿⠟⢻⡿⠿⣿⠯⢿⣿⣿⣿⣿⣿⣿⠛⢿⠁⢻⣾⡀⣉⣿⣿⣿⣿⣿⣿⣿\r\n"
		"⣿⣿⣿⣿⣿⣿⣿⣧⣧⢸⢸⠀⢸⠀⠀⠁⠀⢿⠀⢸⣿⠏⢹⡟⠀⣿⠀⢸⠀⣿⢹⣄⣿⣿⣿⣿⣿⣿⣿⣿\r\n"
		"⣿⣿⣿⣿⣿⣿⣿⣿⣿⣿⢸⡄⠘⠀⠀⠀⠀⣼⠀⠀⣿⠀⢨⡀⠀⢿⠀⢸⠀⣿⠘⢻⣿⣿⣿⣿⣿⣿⣿⣿\r\n"
		"⣿⣿⣿⣿⣿⣿⣿⣿⣿⣿⣿⣧⢸⡀⢸⡄⠀⣧⠀⢘⣿⠀⠀⣧⠀⢸⠀⣸⣸⣿⢿⣿⣿⣿⣿⣿⣿⣿⣿⣿\r\n"
		"⣿⣿⣿⣿⣿⣿⣿⣿⣿⣿⢿⣿⣿⣷⣸⣧⠀⣿⠀⢸⣿⡇⢠⡿⠀⣼⣻⣿⣿⠉⣾⣿⣿⣿⣿⣿⣿⣿⣿⣿\r\n"
		"⣿⣿⣿⣿⣿⣿⣿⣿⣿⡿⢸⣿⣿⣿⣿⣿⡆⣿⣆⢸⣿⡇⣼⡇⣸⣿⣿⣿⡟⠛⣿⣿⣿⣿⣿⣿⣿⣿⣿⣿\r\n"
		"⣿⣿⣿⣿⣿⣿⣿⣿⣿⣄⠀⣹⣿⣿⣿⣿⣿⣿⣿⣾⣿⣷⣿⣇⣿⣿⣿⣿⣿⣤⣿⣿⣿⣿⣿⣿⣿⣿⣿⣿\r\n"
		"⣿⣿⣿⣿⣿⣿⣿⣿⣿⣧⠀⠛⣿⣿⣿⣿⣿⣿⣿⣿⣿⣇⣿⣿⣿⣿⣿⡿⠙⠉⣿⣿⣿⣿⣿⣿⣿⣿⣿⣿\r\n"
		"⣿⣿⣿⣿⣿⣿⣿⣿⣿⣿⡇⠀⢿⣿⣿⣿⣿⣿⣿⣿⣿⣿⣿⣿⣿⣿⣿⣷⠀⢀⣿⣿⣿⣿⣿⣿⣿⣿⣿⣿\r\n"
		"⣿⣿⣿⣿⣿⣿⣿⣿⣿⣏⣷⠀⢸⢻⣿⢹⣿⣿⣿⢻⣿⣿⣿⣿⣿⣿⣿⠙⠀⢘⣿⣿⣿⣿⣿⣿⣿⣿⣿⣿\r\n"
		"⣿⣿⣿⣿⣿⣿⣿⣿⣿⣿⣿⡟⡏⠀⢿⢸⣿⣿⡟⢸⣿⣿⣿⡇⣿⣿⠹⠀⢠⣾⣿⣿⣿⣿⣿⣿⣿⣿⣿⣿\r\n"
		"⣿⣿⣿⣿⣿⣿⣿⣿⣿⣿⣿⣿⣷⣀⣸⠸⡏⢿⣇⠀⡙⠋⣿⡇⢸⡏⡇⠀⣾⣿⣿⣿⣿⣿⣿⣿⣿⣿⣿⣿\r\n"
		"⣿⣿⣿⣿⣿⣿⣿⣿⣿⣿⣿⡇⣿⡟⢹⠀⠁⠸⡇⠀⣤⠀⢿⠀⠸⠁⣆⣠⣿⣿⣿⣿⣿⣿⣿⣿⣿⣿⣿⣿\r\n"
		"⣿⣿⣿⣿⣿⣿⣿⣿⣿⣿⣿⣷⣿⣷⣾⣄⣷⠀⣷⠀⣿⠀⢸⡇⣆⣰⣿⣿⣿⣿⣿⣿⣿⣿⣿⣿⣿⣿⣿⣿\r\n"
		"⣿⣿⣿⣿⣿⣿⣿⣿⣿⣿⣿⣿⣿⣿⣿⣿⣿⣧⣿⣤⣿⣧⣾⣿⣿⣿⣿⣿⣿⣿⣿⣿⣿⣿⣿⣿⣿⣿⣿⣿\r\n";

// Global YLIDAR X2 handler
h_YLIDARX2_t hlidar;

// Global Motors handler
h_Motor_t hMotors;

// Global ToF sensors handler
h_GP2Y0A41SK0F_t hTof;

// Global ADXL343 (Accelerometer) handler
h_ADXL343_t hADXL;

// Task handles
TaskHandle_t xMotors;
TaskHandle_t xControl;
SemaphoreHandle_t xMutex;

// Buttons variables
volatile uint8_t buttonStartPressed = 1; /**< Flag to indicate button press state */

/* USER CODE END PV */

void SystemClock_Config(void);
void MX_FREERTOS_Init(void);
/* USER CODE BEGIN 0 */
/**
 * @brief Transmit a character over UART.
 * @param ch: Character to transmit.
 * @retval int: The transmitted character.
 */
int __io_putchar(int ch)
{
	HAL_UART_Transmit(&huart1, (uint8_t*)&ch, 1, HAL_MAX_DELAY);

	return ch;
}

/**
 * @brief Interrupt callbacks.
 * @details Contains interrupt service routines (ISRs) and related callbacks.
 */

/**
 * @brief UART receive half-complete callback.
 * @param huart: Pointer to the UART handle.
 * @retval None
 * @details This callback processes partial DMA reception for the UART instance
 * (e.g., used for YLIDAR data).
 */
void HAL_UART_RxHalfCpltCallback(UART_HandleTypeDef *huart) {
	if (huart->Instance == USART2) {
		YLIDARX2_ProcessDMAHalfComplete(&hlidar);
	}
}

/**
 * @brief UART receive complete callback.
 * @param huart: Pointer to the UART handle.
 * @retval None
 * @details This callback processes complete DMA reception for the UART instance.
 */
void HAL_UART_RxCpltCallback(UART_HandleTypeDef *huart) {
	if (huart->Instance == USART2) {
		YLIDARX2_ProcessDMAComplete(&hlidar);
	}
}

/**
 * @brief GPIO interrupt callback for EXTI line.
 * @param GPIO_Pin: The GPIO pin that triggered the interrupt.
 * @retval None
 * @details This callback handles the interrupt triggered by the accelerometer
 * (single tap or other configured events).
 */
void HAL_GPIO_EXTI_Callback(uint16_t GPIO_Pin)
{
	if (GPIO_Pin == AG_INT1_Pin) // Interrupt triggered by INT1
	{
		uint8_t int_source;
		ADXL343_readRegister(ADXL343_INT_SOURCE, &int_source, 1);

		if (int_source & 0x40) // Check SINGLE_TAP bit
		{
			DEBUG_PRINT("Single Tap Detected!\n");
			Motor_Stop(&hMotors);
			vTaskDelete(xControl);
		}
	}
	else if (GPIO_Pin == AG_INT2_Pin) // Interrupt triggered by INT2
	{
		DEBUG_PRINT("Interrupt triggered on INT2\n");
		// Handle other potential events from INT2 if needed
	}
	else if (GPIO_Pin == BTN_START_Pin)	// Check if the interrupt is from BTN_START
	{
		static uint32_t last_interrupt_time = 0;
		uint32_t current_time = HAL_GetTick();

		// Debounce handling
		if ((current_time - last_interrupt_time) > DEBOUNCE_DELAY_MS) {
			buttonStartPressed++; // Set flag for button press
			last_interrupt_time = current_time;
		}
	}
}

/**
 * @brief Task declarations.
 * @details Contains declarations for FreeRTOS tasks in the system.
 */

/**
 * @brief Motor control task.
 * @param unsused: Unused parameter.
 * @retval None
 * @details This FreeRTOS task continuously updates the motor speed based on current settings.
 */
void task_Motors(void * unsused)
{
	DEBUG_PRINT("task_Motors\r\n");

	while (1)
	{
		GP2Y0A41SK0F_get_distance(&hTof);
		Motor_UpdateSpeed(&hMotors);

		vTaskDelay(1);
	}
}

/**
 * @brief Behavior control task.
 * @param unsused: Unused parameter.
 * @retval None
 * @details This FreeRTOS task controls motor behavior based on ToF sensor readings.
 * It evaluates distances from ToF sensors and adjusts motor directions accordingly.
 */
void task_Control(void * unsused)
{
	DEBUG_PRINT("task_Control\r\n");

	while (1)
	{
		DEBUG_PRINT("ToF1 distance: %d mm, ToF2 distance: %d mm\r\n", hTof.distance_tof1, hTof.distance_tof2);

		/* Motors test */
		if (hTof.distance_tof2 > TOF_TRESHHOLD && hTof.distance_tof1 > TOF_TRESHHOLD)
		{
			hMotors.mode_mot1 = FORWARD_MODE;
			hMotors.mode_mot2 = FORWARD_MODE;
		}
		else if (hTof.distance_tof2 > TOF_TRESHHOLD && hTof.distance_tof1 <= TOF_TRESHHOLD)
		{
			hMotors.mode_mot1 = FORWARD_MODE;
			hMotors.mode_mot2 = REVERSE_MODE;
		}
		else if (hTof.distance_tof2 <= TOF_TRESHHOLD && hTof.distance_tof1 > TOF_TRESHHOLD)
		{
			hMotors.mode_mot1 = REVERSE_MODE;
			hMotors.mode_mot2 = FORWARD_MODE;
		}
		else //if (hTof.distance_tof2 <= TOF_TRESHHOLD && hTof.distance_tof1 <= TOF_TRESHHOLD)
		{
			hMotors.mode_mot1 = REVERSE_MODE;
			hMotors.mode_mot2 = REVERSE_MODE;
		}

		Motor_SetMode(&hMotors);
		Motor_SetSpeed_percent(&hMotors, 40, 40);
		DEBUG_PRINT("Mot1 speed: %d, Mot2 speed: %d\r\n", hMotors.current_speed1, hMotors.current_speed2);

		vTaskDelay(1);
	}
}

/**
 * @brief Handles errors during task creation.
 * @param r: Return value from xTaskCreate.
 * @retval None
 * @details This function checks the return value of `xTaskCreate` to determine
 * if a task was created successfully. In case of failure, it performs error handling.
 */
void errHandler_xTaskCreate(BaseType_t r)
{
	/* Vérification si la tâche a été créée avec succès */
	if (pdPASS == r) {
		/* Si la tâche est créée avec succès, démarrer le scheduler */
		DEBUG_PRINT("Tâche crée avec succès\r\n");
	} else if (errCOULD_NOT_ALLOCATE_REQUIRED_MEMORY == r) {
		DEBUG_PRINT("Erreur: Mémoire insuffisante\r\n");
		Error_Handler();
	} else {
		/* Cas improbable : code d'erreur non prévu pour xTaskCreate */
		DEBUG_PRINT("Erreur inconnue lors de la création de la tâche\r\n");
		Error_Handler();  	// Gestion d'erreur générique
		NVIC_SystemReset(); // Réinitialiser le microcontrôleur
	}
}

/* USER CODE END 0 */

/**
 * @brief  The application entry point.
 * @retval int
 */
int main(void)
{

	/* USER CODE BEGIN 1 */
	BaseType_t xReturned;

	/* USER CODE END 1 */

	/* MCU Configuration--------------------------------------------------------*/

	/* Reset of all peripherals, Initializes the Flash interface and the Systick. */
	HAL_Init();

	/* Configure the system clock */
	SystemClock_Config();

	/* USER CODE BEGIN SysInit */
	/**
	 * @brief Peripheral initialization.
	 * @details Contains initialization code for GPIO, ADC, SPI, TIM, etc.
	 */
	/* USER CODE END SysInit */

	/* Initialize all configured peripherals */
	MX_GPIO_Init();
	MX_DMA_Init();
	MX_SPI1_Init();
	MX_TIM1_Init();
	MX_TIM3_Init();
	MX_TIM4_Init();
	MX_USART2_UART_Init();
	MX_USART1_UART_Init();
	MX_ADC1_Init();
	/* USER CODE BEGIN 2 */
	DEBUG_PRINT("\r\n*** Waking up V-NOM ***\r\n");
	DEBUG_PRINT("%s", jumbo_logo_msg);

	/* ToF sensors Initialization */
	GP2Y0A41SK0F_Init(&hTof);

	/* ADXL343 Initialization */
	ADXL343_Init(&hADXL);

	/* Motors Initialization */
	Motor_Init(&hMotors, &htim1);

	/* YLIDAR X2 Initialization with DMA */
	LIDAR_RX_GPIO_Port->PUPDR = GPIO_PULLUP;
	YLIDARX2_InitDMA(&hlidar, &huart2);

	xMutex = xSemaphoreCreateMutex();
	if (xMutex == NULL) {
		printf("Erreur lors de la création du Mutex\r\n");
		Error_Handler();
	}

	/* Motors task */
	xReturned = xTaskCreate(
			task_Motors, // Function that implements the task.
			"task_Motors", // Text name for the task.
			STACK_SIZE, // Stack size in words, not bytes.
			(void *) 0, // Parameter passed into the task.
			TASK_PRIORITY_MOTOR,// Priority at which the task is created.
			&xMotors); // Used to pass out the created task's handle.

	errHandler_xTaskCreate(xReturned);

	/* Control task */
	xReturned = xTaskCreate(
			task_Control, // Function that implements the task.
			"task_Control", // Text name for the task.
			STACK_SIZE, // Stack size in words, not bytes.
			(void *) 0, // Parameter passed into the task.
			TASK_PRIORITY_CONTROL,// Priority at which the task is created.
			&xControl); // Used to pass out the created task's handle.

	errHandler_xTaskCreate(xReturned);

	/* USER CODE END 2 */

	/* Call init function for freertos objects (in cmsis_os2.c) */
	MX_FREERTOS_Init();

	/* Start scheduler */
	osKernelStart();

	/* We should never get here as control is now taken by the scheduler */

	/* Infinite loop */
	/* USER CODE BEGIN WHILE */
	while (1)
	{
		/* ADXL343 test *
		ADXL343_get_Acceleration(&hADXL);*/

		/* USER CODE END WHILE */

		/* USER CODE BEGIN 3 */
	}
	/* USER CODE END 3 */
}

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
/* USER CODE BEGIN 4 */

/**
 * @brief UART error callback.
 * @param huart: Pointer to the UART handle.
 * @retval None
 * @details This function handles UART errors such as parity, noise, framing,
 * or overrun errors. It restarts the LIDAR's DMA in case of errors.
 */
void HAL_UART_ErrorCallback(UART_HandleTypeDef *huart)
{
	if (huart->Instance == USART2)
	{
		if (HAL_UART_GetError(huart) & HAL_UART_ERROR_PE)
			DEBUG_PRINT("Parity Error!\r\n");
		if (HAL_UART_GetError(huart) & HAL_UART_ERROR_NE)
			DEBUG_PRINT("Noise Error!\r\n");
		if (HAL_UART_GetError(huart) & HAL_UART_ERROR_FE)
			DEBUG_PRINT("Framing Error!\r\n");
		if (HAL_UART_GetError(huart) & HAL_UART_ERROR_ORE)
			DEBUG_PRINT("Overrun Error!\r\n");

		//YLIDARX2_RestartDMA(&hlidar);
	}
}

/* USER CODE END 4 */

/**
 * @brief  Period elapsed callback in non blocking mode
 * @note   This function is called  when TIM2 interrupt took place, inside
 * HAL_TIM_IRQHandler(). It makes a direct call to HAL_IncTick() to increment
 * a global variable "uwTick" used as application time base.
 * @param  htim : TIM handle
 * @retval None
 */
void HAL_TIM_PeriodElapsedCallback(TIM_HandleTypeDef *htim)
{
	if (htim->Instance == TIM2) {
		HAL_IncTick();
	}
}

/**
 * @brief  This function is executed in case of error occurrence.
 * @retval None
 */
void Error_Handler(void)
{
	/* USER CODE BEGIN Error_Handler_Debug */
	/* User can add his own implementation to report the HAL error return state */
	__disable_irq();
	while (1)
	{
	}
	/* USER CODE END Error_Handler_Debug */
}

#ifdef  USE_FULL_ASSERT
/**
 * @brief  Reports the name of the source file and the source line number
 *         where the assert_param error has occurred.
 * @param  file: pointer to the source file name
 * @param  line: assert_param error line source number
 * @retval None
 */
void assert_failed(uint8_t *file, uint32_t line)
{
	/* USER CODE BEGIN 6 */
	/* User can add his own implementation to report the file name and line number,
     ex: printf("Wrong parameters value: file %s on line %d\r\n", file, line) */
	/* USER CODE END 6 */
}
#endif /* USE_FULL_ASSERT */

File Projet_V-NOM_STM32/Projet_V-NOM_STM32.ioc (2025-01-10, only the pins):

Mcu.UserName=STM32G431CBUx
PA0.GPIO_Label=ToF2
PA0.Signal=SharedAnalog_PA0
PA10.Signal=S_TIM1_CH3
PA11.Signal=S_TIM4_CH1
PA12.Signal=S_TIM4_CH2
PA13.Signal=SYS_JTMS-SWDIO
PA14.Signal=SYS_JTCK-SWCLK
PA15.GPIO_Label=LIDAR_RX
PA15.Signal=USART2_RX
PA2.Signal=ADC1_IN3
PA3.GPIO_Label=AG_INT1
PA3.Signal=GPXTI3
PA4.GPIO_Label=AG_INT2
PA4.Signal=GPXTI4
PA5.Signal=SPI1_SCK
PA6.Signal=SPI1_MISO
PA7.Signal=SPI1_MOSI
PA8.Signal=S_TIM1_CH1
PA9.Signal=S_TIM1_CH2
PB0.GPIO_Label=LED_RED
PB0.Signal=GPIO_Output
PB1.GPIO_Label=LED_GREEN
PB1.Signal=GPIO_Output
PB13.Signal=TIM1_CH1N
PB14.Signal=TIM1_CH2N
PB3.GPIO_Label=LIDAR_TX
PB3.Signal=USART2_TX
PB4.Signal=S_TIM3_CH1
PB5.Signal=S_TIM3_CH2
PB6.GPIO_Label=VCP_TX
PB6.Signal=USART1_TX
PB7.GPIO_Label=VCP_RX
PB7.Signal=USART1_RX
PB9.GPIO_Label=BTN_MODE
PB9.Signal=GPIO_Input
PC10.GPIO_Label=EN_LIDAR
PC10.Signal=GPIO_Output
PC11.GPIO_Label=EN_MOT
PC11.Signal=GPIO_Output
PC13.GPIO_Label=BTN_START
PC13.Signal=GPIO_Input
PC14-OSC32_IN.Signal=RCC_OSC32_IN
PC15-OSC32_OUT.Signal=RCC_OSC32_OUT
PC4.GPIO_Label=SPI1_CSN
PC4.Signal=GPIO_Output
PF0-OSC_IN.Signal=RCC_OSC_IN
PF1-OSC_OUT.Signal=RCC_OSC_OUT

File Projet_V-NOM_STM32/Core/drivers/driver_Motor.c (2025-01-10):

/**
 * @file motor_control.c
 * @brief Motor control implementation for initializing, setting modes, controlling speed, and updating motor states.
 */

#include "driver_Motor.h"
#include "tim.h"  // Inclusion for access to timers
#include <stdio.h>

#define DEBUG 0 /**< Enable or disable debug logs */

#if DEBUG
#define DEBUG_PRINT(...) printf(__VA_ARGS__)
#else
#define DEBUG_PRINT(...)
#endif


/**
 * @brief Initialize the motors.
 * @param hMotors Pointer to the motor handle structure.
 * @param htim Pointer to the timer handle used for PWM control.
 */
void Motor_Init(h_Motor_t * hMotors, TIM_HandleTypeDef * htim) {
	// Allows to get direct parameters from the timer used
	hMotors->htim = htim;
	hMotors->speed_increase_rate1 = 50;
	hMotors->speed_increase_rate2 = 50;

	__HAL_RCC_GPIOA_CLK_ENABLE();
	__HAL_RCC_GPIOB_CLK_ENABLE();

	MX_TIM1_Init();
	//MX_TIM2_Init();

	HAL_TIM_PWM_Start(hMotors->htim, TIM_CHANNEL_1);
	HAL_TIM_PWM_Start(hMotors->htim, TIM_CHANNEL_2);
	HAL_TIMEx_PWMN_Start(hMotors->htim, TIM_CHANNEL_1);
	HAL_TIMEx_PWMN_Start(hMotors->htim, TIM_CHANNEL_2);

	hMotors->mode_mot1 = STANDBY_MODE;
	hMotors->mode_mot2 = STANDBY_MODE;
	Motor_SetMode(hMotors);
}

/**
 * @brief Set the operating mode of the motors.
 * @param hMotors Pointer to the motor handle structure.
 */
void Motor_SetMode(h_Motor_t * hMotors)
{
	switch (hMotors->mode_mot1) {
	case FORWARD_MODE:
		DEBUG_PRINT("Mot1: FORWARD_MODE\r\n");
		HAL_TIM_PWM_Start(hMotors->htim, TIM_CHANNEL_1);
		HAL_TIMEx_PWMN_Stop(hMotors->htim, TIM_CHANNEL_1);
		break;

	case REVERSE_MODE:
		DEBUG_PRINT("Mot1: REVERSE_MODE\r\n");
		HAL_TIMEx_PWMN_Start(hMotors->htim, TIM_CHANNEL_1);
		HAL_TIM_PWM_Stop(hMotors->htim, TIM_CHANNEL_1);
		break;

	case STANDBY_MODE:
	default:
		HAL_TIMEx_PWMN_Stop(hMotors->htim, TIM_CHANNEL_1);
		HAL_TIM_PWM_Stop(hMotors->htim, TIM_CHANNEL_1);
		__HAL_TIM_SET_COMPARE(hMotors->htim, TIM_CHANNEL_1, 0);
		break;
	}

	switch (hMotors->mode_mot2) {
	case FORWARD_MODE:
		DEBUG_PRINT("Mot2: FORWARD_MODE\r\n");
		HAL_TIM_PWM_Start(hMotors->htim, TIM_CHANNEL_2);
		HAL_TIMEx_PWMN_Stop(hMotors->htim, TIM_CHANNEL_2);
		break;

	case REVERSE_MODE:
		DEBUG_PRINT("Mot2: REVERSE_MODE\r\n");
		HAL_TIMEx_PWMN_Start(hMotors->htim, TIM_CHANNEL_2);
		HAL_TIM_PWM_Stop(hMotors->htim, TIM_CHANNEL_2);
		break;

	case STANDBY_MODE:
	default:
		HAL_TIMEx_PWMN_Stop(hMotors->htim, TIM_CHANNEL_2);
		HAL_TIM_PWM_Stop(hMotors->htim, TIM_CHANNEL_2);
		__HAL_TIM_SET_COMPARE(hMotors->htim, TIM_CHANNEL_2, 0);
		break;
	}
}

/**
 * @brief Set the speed of the motors as a percentage of maximum speed.
 * @param hMotor Pointer to the motor handle structure.
 * @param percent1 Speed percentage for motor 1 (0.0 to 100.0).
 * @param percent2 Speed percentage for motor 2 (0.0 to 100.0).
 */
void Motor_SetSpeed_percent(h_Motor_t * hMotor, float percent1, float percent2) {
	hMotor->speed1 = (int)(MOTOR1_REV_DIFF * hMotor->htim->Init.Period * percent1/100.0);
	hMotor->speed2 = (int)(hMotor->htim->Init.Period * percent2/100.0);
}

/**
 * @brief Stop all motors by setting their mode to standby.
 * @param hMotor Pointer to the motor handle structure.
 */
void Motor_Stop(h_Motor_t * hMotors) {
	hMotors->mode_mot1 = STANDBY_MODE;
	hMotors->mode_mot2 = STANDBY_MODE;
	Motor_SetMode(hMotors);
}

/**
 * @brief Update motor speeds gradually to achieve smoother transitions.
 * @param hMotor Pointer to the motor handle structure.
 */
void Motor_UpdateSpeed(h_Motor_t * hMotors) {
	// Increase speed progressively
	if (hMotors->speed1 > hMotors->current_speed1)
		hMotors->current_speed1 += hMotors->speed_increase_rate1;
	if (hMotors->speed2 > hMotors->current_speed2)
		hMotors->current_speed2 += hMotors->speed_increase_rate2;

	// Decrease speed progressively
	if (hMotors->speed1 < hMotors->current_speed1)
		hMotors->current_speed1 -= hMotors->speed_increase_rate1;
	if (hMotors->speed2 < hMotors->current_speed2)
		hMotors->current_speed2 -= hMotors->speed_increase_rate2;

	__HAL_TIM_SET_COMPARE(hMotors->htim, TIM_CHANNEL_1, hMotors->current_speed1);
	__HAL_TIM_SET_COMPARE(hMotors->htim, TIM_CHANNEL_2, hMotors->current_speed2);
}

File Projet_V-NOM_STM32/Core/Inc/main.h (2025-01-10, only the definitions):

#define BTN_START_Pin GPIO_PIN_13
#define BTN_START_GPIO_Port GPIOC
#define ToF2_Pin GPIO_PIN_0
#define ToF2_GPIO_Port GPIOA
#define AG_INT1_Pin GPIO_PIN_3
#define AG_INT1_GPIO_Port GPIOA
#define AG_INT2_Pin GPIO_PIN_4
#define AG_INT2_GPIO_Port GPIOA
#define SPI1_CSN_Pin GPIO_PIN_4
#define SPI1_CSN_GPIO_Port GPIOC
#define LED_RED_Pin GPIO_PIN_0
#define LED_RED_GPIO_Port GPIOB
#define LED_GREEN_Pin GPIO_PIN_1
#define LED_GREEN_GPIO_Port GPIOB
#define LIDAR_RX_Pin GPIO_PIN_15
#define LIDAR_RX_GPIO_Port GPIOA
#define EN_LIDAR_Pin GPIO_PIN_10
#define EN_LIDAR_GPIO_Port GPIOC
#define EN_MOT_Pin GPIO_PIN_11
#define EN_MOT_GPIO_Port GPIOC
#define LIDAR_TX_Pin GPIO_PIN_3
#define LIDAR_TX_GPIO_Port GPIOB
#define VCP_TX_Pin GPIO_PIN_6
#define VCP_TX_GPIO_Port GPIOB
#define VCP_RX_Pin GPIO_PIN_7
#define VCP_RX_GPIO_Port GPIOB
#define BTN_MODE_Pin GPIO_PIN_9
#define BTN_MODE_GPIO_Port GPIOB

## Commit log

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2024-09-18 Projet KiCAD vierge
    [EDI2CAP.CFG, MP1475SGJ-P.SchLib, MP1475SGJ-P.stp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]
2024-09-18 Ajout de la bonne empreinte BU33SD5WG-TR
    [BU33SD5WG-TR.SchLib, BU33SD5WG-TR.stp, EDI2CAP.CFG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]
2024-09-18 Création de la page controle
    [Pojet_V-NOM_KiCAD.kicad_sch, controle.kicad_sch]
2024-09-18 Empreinte du STM32G431CBU6
    [EDI2CAP.CFG, QFN50P700X700X65-49N-D.PcbLib, STM32G431CBU6.SchLib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]
2024-09-18 Mise à jour du schéma éléctrique
    [controle.kicad_sch]
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2024-09-25 Pins configurés projet STM32CubeIDE
    [controle.kicad_sch]
2024-09-30 Drivers
    schéma drivers
    [Pojet_V-NOM_KiCAD.kicad_sch, deplacement.kicad_sch]
2024-09-30 alimentation
    ajout alimentation
    [Pojet_V-NOM_KiCAD.kicad_sch, alimentation.kicad_sch]
2024-09-30 Ajout de toutes les feuilles au projet principal
    [Pojet_V-NOM_KiCAD.kicad_sch, acquisition.kicad_sch, alimentation.kicad_sch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]
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2024-09-30 lidar
    rajout du lidar
    [acquisition.kicad_sch]
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2024-10-01 Fonctions Pins
    [interface_utilisateur.kicad_sch]
2024-10-01 rajout capteur
    capteur de bordure
    [acquisition.kicad_sch, alimentation.kicad_sch, deplacement.kicad_sch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]
2024-10-01 regulateur 5 V
    Regulateur 5V maj
    [alimentation.kicad_sch]
2024-10-01 MAJ Valerian
    MAJ Valerian
    [acquisition.kicad_sch, alimentation.kicad_sch, deplacement.kicad_sch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]
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2024-10-01 Mise à jour des pins
    [controle.kicad_sch]
2024-10-01 Mise à jour partie controle
    [controle.kicad_sch]
2024-10-01 Import Pins UI
    [Pojet_V-NOM_KiCAD.kicad_sch, interface_utilisateur.kicad_sch]
2024-10-01 Pins controle sortis
    [Pojet_V-NOM_KiCAD.kicad_sch, interface_utilisateur.kicad_sch]
2024-10-01 Links UI première partie
    [Pojet_V-NOM_KiCAD.kicad_sch]
2024-10-01 Revert "Links UI première partie"
    This reverts commit fbbc2c843fcae622b23db25f047c9362e448de8c.
    [Pojet_V-NOM_KiCAD.kicad_sch]
2024-10-01 Link Pins UI
    Les Pins qui ne sont pas encore liés n'ont pas de pins correspondants
    sur la partie controle. Il faut les créer (les deux leds rouge/verte) et
    demander au prof pour NRST et SWO
    [Pojet_V-NOM_KiCAD.kicad_sch]
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2024-10-01 Maj Deplacement
    Maj Deplacement
    [Driver_Moter.kicad_sch, Pojet_V-NOM_KiCAD.kicad_sch, deplacement.kicad_sch]
2024-10-01 Directions des liaisons UI
    [Pojet_V-NOM_KiCAD.kicad_sch]
2024-10-01 Schéma de contrôle mis à jour
    [controle.kicad_sch]
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2024-10-01 Mise à jour du schéma KiCAD
    [Pojet_V-NOM_KiCAD.kicad_sch]
2024-10-01 Mise à jour du schéma de contrôle
    [Pojet_V-NOM_KiCAD.kicad_sch, controle.kicad_sch]
2024-10-01 Mise à jour du schéma principal
    [Pojet_V-NOM_KiCAD.kicad_sch, controle.kicad_sch]
2024-10-01 Maj
    Maj lidar et regualteur
    [Pojet_V-NOM_KiCAD.kicad_sch, Régulateur_3.3V.kicad_sch, Régulateur_5V.kicad_sch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]
2024-10-01 Retouches lisibilité Alim / capteurs
    [Régulateur_3.3V.kicad_sch, Régulateur_5V.kicad_sch, acquisition.kicad_sch]
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2024-10-02 Correction schéma accéléromètre
    [Pojet_V-NOM_KiCAD.kicad_sch, acquisition.kicad_sch]
2024-10-02 Ajout des pin d'interruption AG
    [controle.kicad_sch]
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2024-10-02 Branchement final de l'accéléromètre
    [Pojet_V-NOM_KiCAD.kicad_sch]
2024-10-02 maj regulateur 5V
    [Pojet_V-NOM_KiCAD.kicad_sch, Régulateur_5V.kicad_sch, acquisition.kicad_sch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]
2024-10-02 Corrections rapides du schéma global
    [Driver_Moter.kicad_sch, Pojet_V-NOM_KiCAD.kicad_sch, controle.kicad_sch]
2024-10-02 Corrections sonde et switch
    [alimentation.kicad_sch, interface_utilisateur.kicad_sch]
2024-10-02 Correction du schéma global
    [Pojet_V-NOM_KiCAD.kicad_sch]
2024-10-02 DERNIER MODIF Alim
    [Driver_Moter.kicad_sch, Pojet_V-NOM_KiCAD.kicad_sch, Régulateur_3.3V.kicad_sch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]
2024-10-02 Empreinte des bouttons poussoirs
    [430182070816.PcbLib, 430182070816.SchLib, 430182070816.psm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]
2024-10-02 Fix boutons poussoirs + BTN_START
    [Pojet_V-NOM_KiCAD.kicad_sch, interface_utilisateur.kicad_sch]
2024-10-02 Empreinte boutons
    [interface_utilisateur.kicad_sch]
2024-10-02 Modifications conseillés par l'enseignant
    [Pojet_V-NOM_KiCAD.kicad_sch, acquisition.kicad_sch, alimentation.kicad_sch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]
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2024-10-02 Nettoyage des librairies d'empreintes
    [430182070816.PcbLib, 430182070816.SchLib, 430182070816.psm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]
2024-10-03 Correction des erreurs évidentes
    Changements avant vérification des erreurs :
    - Désallocation du pin BTN_RESET
    - Réarrangement de certaines sources pour cohérence avec tous les
    schémas éléctriques
    [Driver_Moter.kicad_sch, Pojet_V-NOM_KiCAD.kicad_sch, acquisition.kicad_sch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]
2024-10-05 point de test et début de placement
    [Driver_Moter.kicad_sch, Pojet_V-NOM_KiCAD.kicad_pcb, Régulateur_3.3V.kicad_sch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]
2024-10-07 maj emplacement
    [Driver_Moter.kicad_sch, Pojet_V-NOM_KiCAD.kicad_pcb, acquisition.kicad_sch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]
2024-10-07 placement des compo dans la pcb
    [Pojet_V-NOM_KiCAD.kicad_pcb]
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2024-10-08 placement maj
    [Driver_Moter.kicad_sch, Pojet_V-NOM_KiCAD.kicad_pcb, Pojet_V-NOM_KiCAD.kicad_sch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]
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2024-10-09 grande partie de routage
    [Pojet_V-NOM_KiCAD.kicad_pcb, acquisition.kicad_sch, deplacement.kicad_sch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]
2024-10-16 création schématique inductance
    [Pojet_V-NOM_KiCAD.kicad_pcb]
2024-10-16 maj routage
    [Pojet_V-NOM_KiCAD.kicad_pcb, Régulateur_5V.kicad_sch, acquisition.kicad_sch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]
2024-10-16 Completion des feuilles de commande
    [2425_ESE_Projet_NOM.ods, 2425_ESE_Projet_V-NOM_BELLIARD_Farnell.ods, 2425_ESE_Projet_V-NOM_BELLIARD_Mouser.ods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]
2024-10-16 Feuille de commande finale
    Feuille de commande nécessaire finale retenue complétée.
    [2425_ESE_Projet_V-NOM_BELLIARD_Farnell.ods, 2425_ESE_Projet_V-NOM_BELLIARD_Mouser.ods, 2425_ESE_Projet_V-NOM_BELLIARD_RS.ods]
2024-10-16 maj routage 24
    [Pojet_V-NOM_KiCAD.kicad_pcb]
2024-10-21 Maj final rootage + logo
    [Pojet_V-NOM_KiCAD.kicad_pcb]
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2024-10-22 maj final aprés correction du prof + logo ensea
    [Pojet_V-NOM_KiCAD.kicad_pcb, controle.kicad_sch]
2024-10-23 Modif
    dernier_Modification
    [Pojet_V-NOM_KiCAD.kicad_pcb]
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2024-12-18 ToF driver fixed & README.md updated
    [driver_GP2Y0A41SK0F.c, driver_YLIDARX2.c, main.c]
2024-12-22 SPI connection fixed: data size set to 8 bits
    [Projet_V-NOM_STM32.ioc, main.c]
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2024-12-22 Final naive drivers for ADXL343
    This new driver is naive since it doesn't handle power saving or data format configuration. It only configures the ADXL343 to expect 4g variations and read the acceleration data.
    [driver_ADXL343.c]
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2025-01-07 Noise Error with the UART2 communication
    [Projet_V-NOM_STM32.ioc, main.c]
2025-01-07 UART2: Framing Error
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2025-01-10 ADC IRQ issue
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2025-01-14 Revert "YLidar X2 DMA driver"
    This reverts commit edcbfe3d9d525ab5c18b018b1decbfc4f346268b.
    [driver_YLIDARX2.c]
